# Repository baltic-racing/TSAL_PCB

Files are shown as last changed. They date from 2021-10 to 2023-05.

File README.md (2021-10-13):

# TSAL - Tractive System Active Light
The TSAL is an optical indicator mounted at the top of the main hoop while being protected by the rollover-envelope. The TSAL indicates the status of the TS.

The TSAL has the following pins:
- 24V power-input
- ground connection
- red and green signal inputs from the TSAC
- red signal input from the HV-Distribution
- green signal output to the Dashboard LED

SCS are adhered to. The TSAL inputs are considered SCS (T11.9) class a (signals transmitted by cable) and hence need to fail in safe mode if the following erros occur:
- Open circuit
- Short circuit to ground
The safe state of the TSAL is all lights being off. The two colors are mutually exclusive. If one color shorts to ground or fails in open circuit, it wont light up causing safe mode. Both devices needing measurement are directly connected to the TSAL. The TSAL performance additional plausibility-checks between DC-bus and TSAC voltages and states and outputs a buffered, plausibility-checked signal for the green LED in the dashboard.

The 2022 rules do *not* require measures against single points of failure causing a massive reduction of effort compared to 2019-2021.

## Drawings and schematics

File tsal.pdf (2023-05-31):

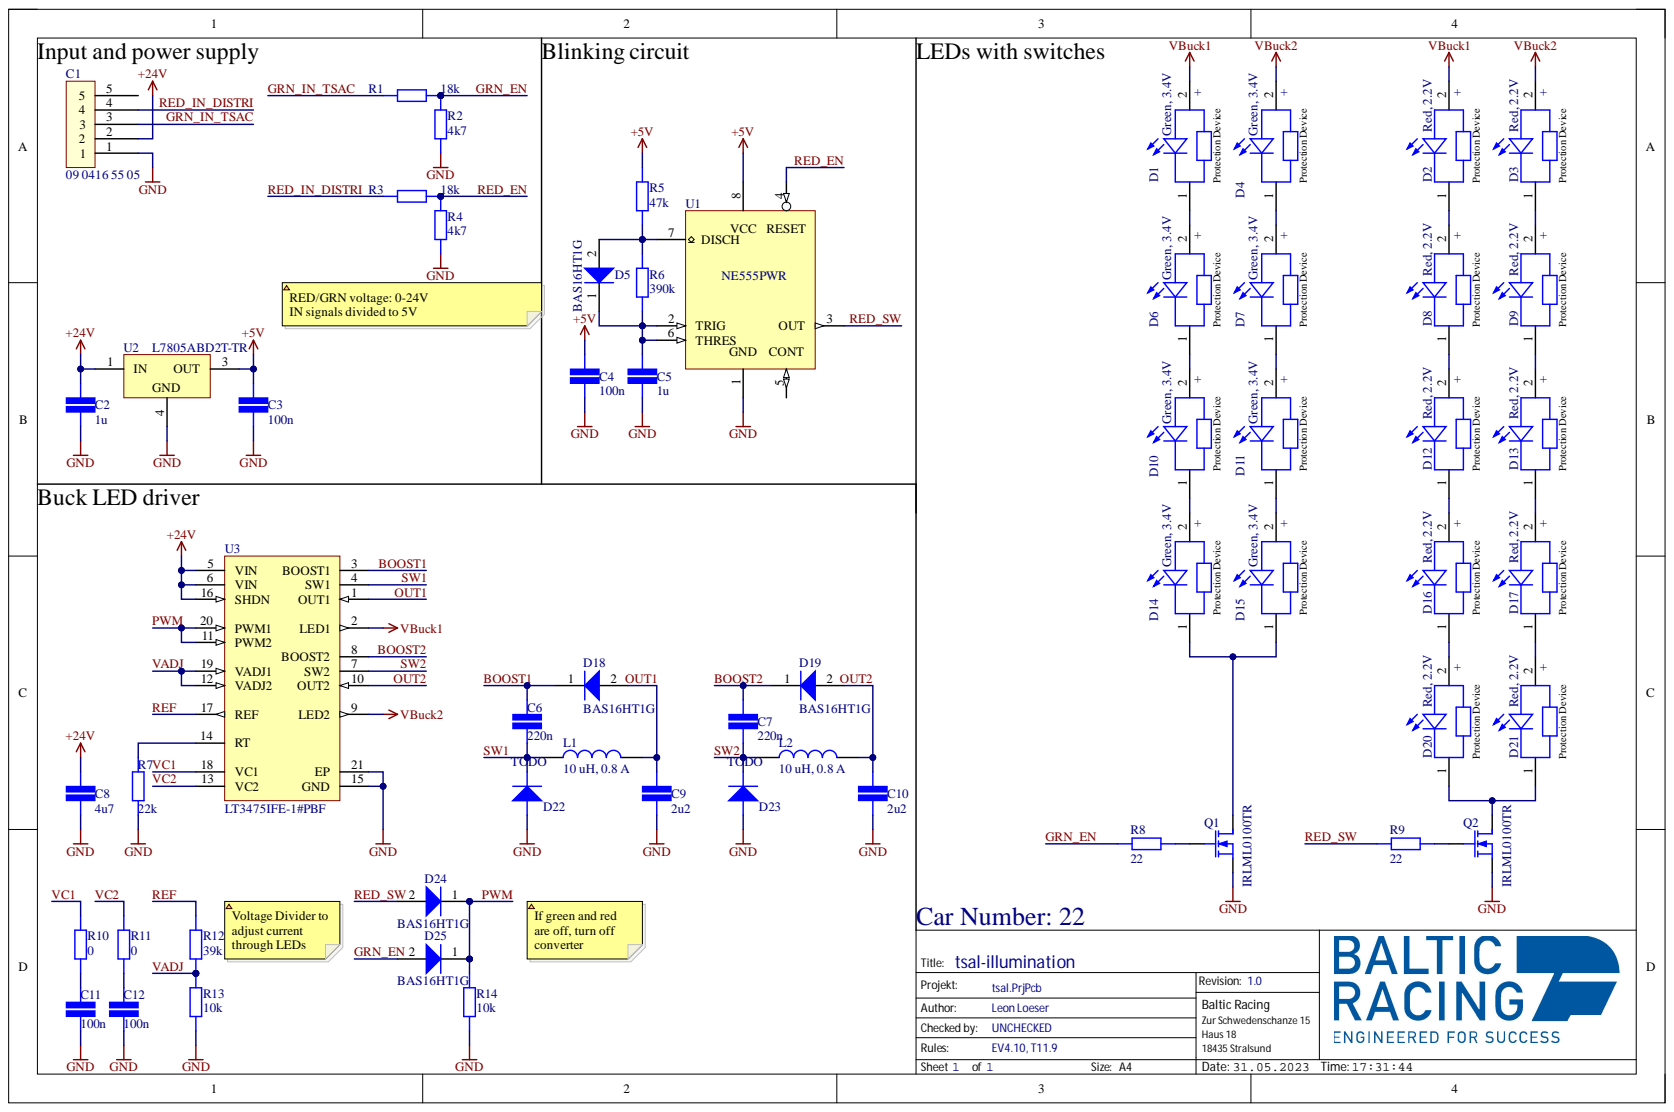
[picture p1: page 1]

3 | GRN _IN _ T S A C

6 | 4 SW 1
1 6 | 1 O U T 1

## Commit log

2021-10-11 Started TSAL project
    [tsal.PrjPcb, tsal.SchDoc]
2021-10-11 Finish layout; add .gitignore to sim; rm artifacts
    [tsal.SchDoc]
2021-10-11 Start layouting PCB; Update LED component
    [tsal.PcbDoc, tsal.PrjPcb, tsal.SchDoc]
2021-10-12 Fix LED position; Layout buck converter
    [tsal.PcbDoc, tsal.SchDoc]
2021-10-13 Add plausibility checks; Add dashboard-signal
    [tsal-illumination.SchDoc, tsal.PcbDoc, tsal.PrjPcb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]
2021-10-13 Finish routing; Ready for review and output-gen
    [tsal-illumination.SchDoc, tsal.PcbDoc, tsal.PrjPcb]
2021-10-13 Fix filename
    [tsal-logic.SchDoc, tsal.PrjPcb]
2021-10-15 Fix ORing; Fix input voltages. Ready for review
    [tsal-logic.SchDoc, tsal.PcbDoc]
2021-10-16 Add baltic logo
    [tsal.PcbDoc]
2021-10-16 Add name and version number
    [tsal.PcbDoc]
2021-12-01 Changed connector, fixed signals; ready2review
    [tsal-illumination.SchDoc, tsal-logic.SchDoc, tsal.PcbDoc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]
2022-01-06 changed angle of the Binder connector to clear mainhoop
    had to modify a few traces and one LED is now crocket so looks like shit but thats how the cookie crumbles.
    [tsal.PcbDoc]
2022-02-05 added Voltage ratings to the CAPS
    [tsal.SchDoc]
2022-02-05 Added Voltage Parameter to CAPS and modified bom outjob to Sort after Voltage
    [tsal.SchDoc]
2022-03-20 Change LDO
    [tsal.PcbDoc, tsal.SchDoc]
2022-05-14 modified PCB
    changed from binder connector to soldered wire due to delivery problems, changed the mounting holes from 3mm to 3.3mm so screw will easy get through rerouted a bit due to clearances added two mounting holes on interface side
    [tsal.PcbDoc]
2022-05-14 add gerber files and little fix on the mounting points
    [tsal.PcbDoc]
2022-05-14 updated gerber files
2022-05-14 updated project file
    [tsal.PrjPcb]
2022-06-13 added board outline and regenerated gerber files
    [tsal.PcbDoc, tsal.PrjPcb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]
2023-05-31 Added car number and schematic export
    [tsal.PrjPcb, tsal.SchDoc]
